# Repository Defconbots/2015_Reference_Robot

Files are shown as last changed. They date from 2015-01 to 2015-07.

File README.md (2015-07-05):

2015_Reference_Robot
====================

The laser used for the contest is the **50 mW** version of this laser: http://www.civillaser.com/532nm-5mw50mw-ttl-modulation-green-laser-module-dot-16mmx70mm-p-130.html

You'll need a controller to run the robot. The source for the controller can be found in the /hw folder.

Software to run the reference robot is in the /sw/TowerDefenderMkII folder.

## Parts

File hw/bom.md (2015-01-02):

## Laser Driver BOM

|Name |Quantity|Part Number |Distributor|
|:---:|:---:|:---:|:---:|
|JP1 |1 |651-5442251 |Mouser |
|IC1 |1 |895-FT232RL |Mouser |
|X1 |1 |538-47346-1001 |Mouser |
|IC2 |1 |998-MIC5219-3.0YMM  |Mouser |
|C1,C2,C3,C4 |4 |C1608X5R1C106M080AB |Mouser |
|C6 |1 |VJ0603A471KXQPW1BC  |Mouser |

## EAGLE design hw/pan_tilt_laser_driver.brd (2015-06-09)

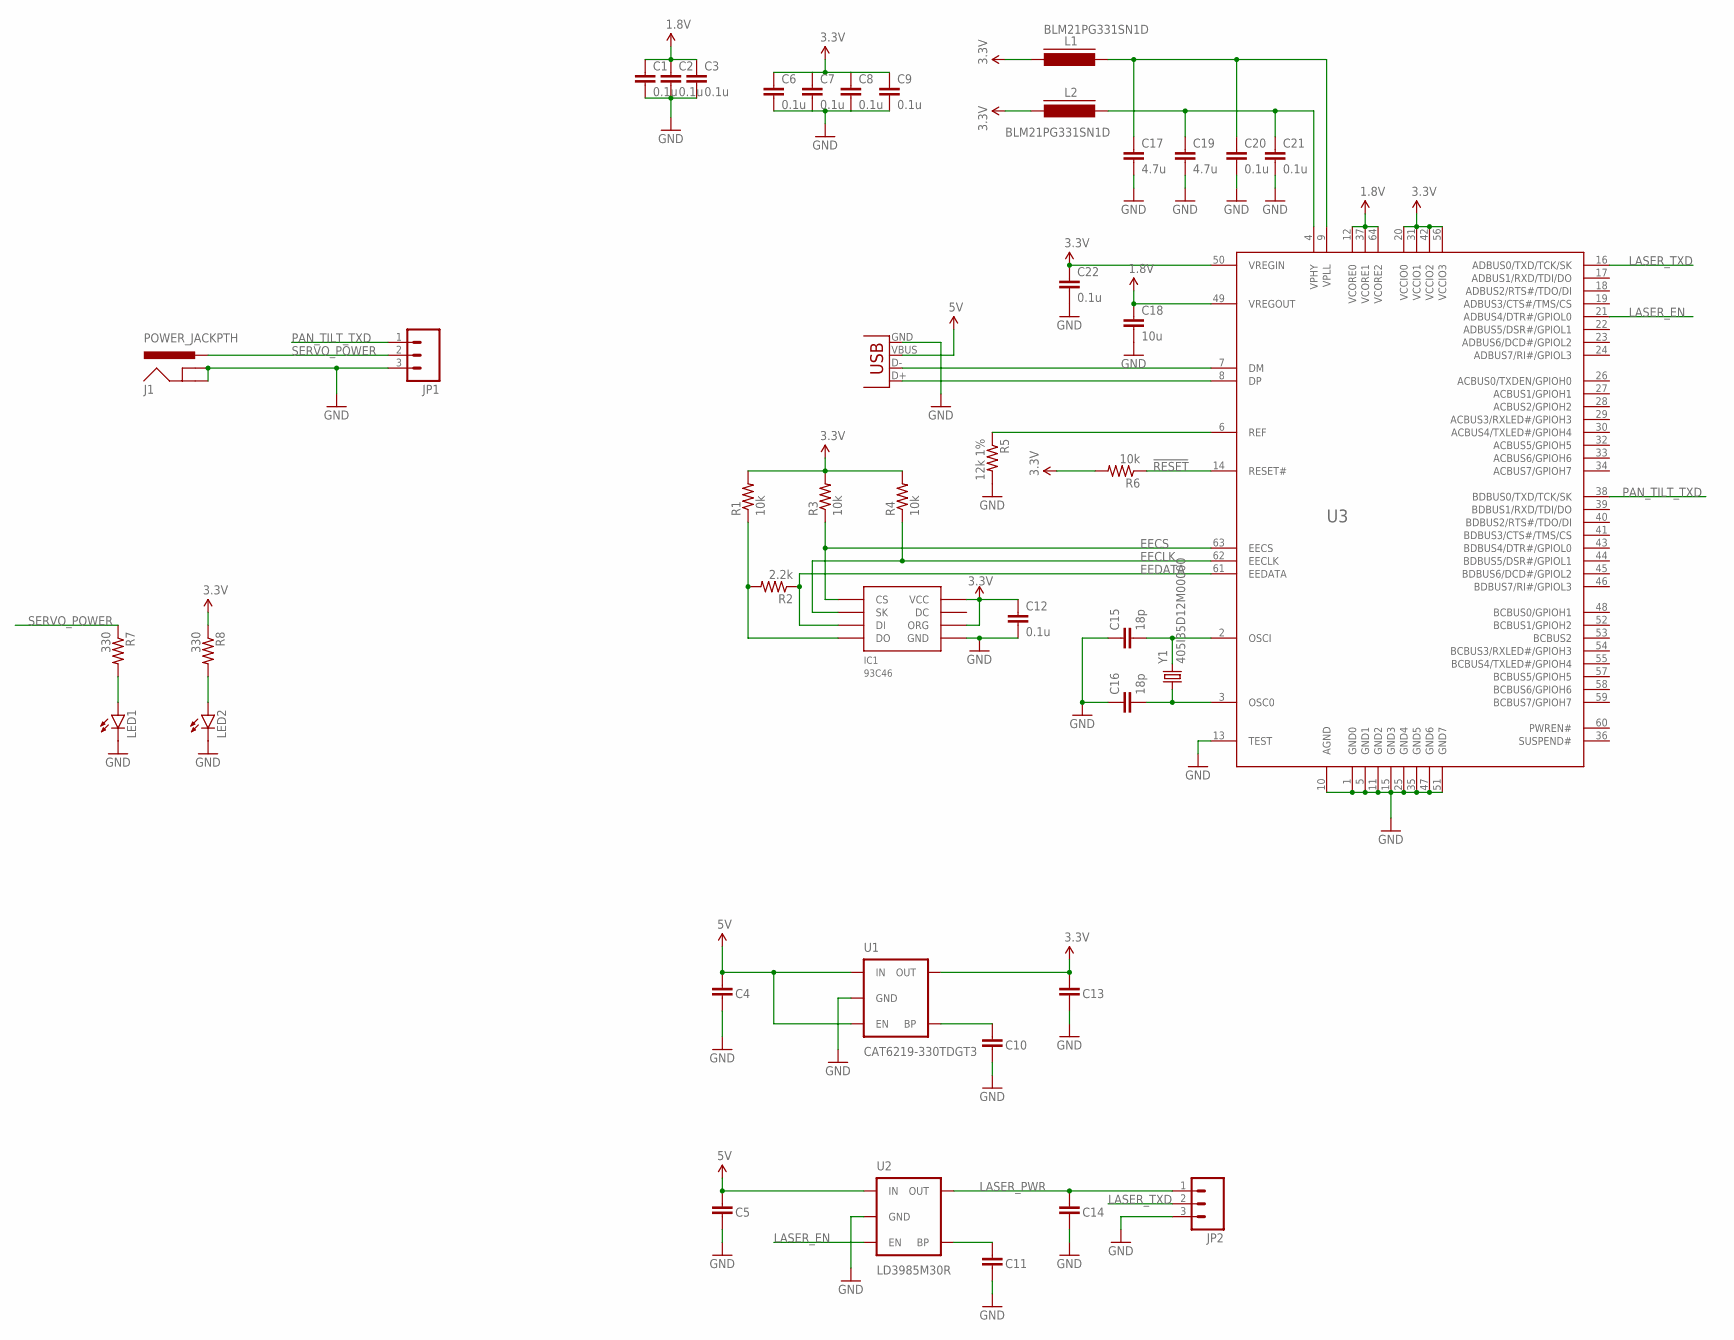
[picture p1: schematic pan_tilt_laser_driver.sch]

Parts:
C1, C2, C3, C6, C7, C8, C9, C12, C20, C21, C22: 0.1u; C0603K
C4, C5, C13, C14: 10u; 0603-CAP
C10, C11: 0.01u; 0603-CAP
C15, C16: 18p; C0603K
C17, C19: 4.7u; C0603K
C18: 10u; C0603K
IC1: 93C46; SOIC8
J1: POWER_JACKPTH; POWER_JACK_PTH
JP1: M0322-03-5035; 22-03-5035
JP2: 651-5442251; SCREWTERMINAL-3.5MM-3
L1, L2: BLM21PG331SN1D; FB805
LED1, LED2: LED1206; LED-1206
R1, R3, R4, R6: 10k; R0603
R2: 2.2k; R0603
R5: 12k 1%; R0603
R7, R8: 330; R0603
U1: CAT6219-330TDGT3; SOT23-5
U2: LD3985M30R; SOT23-5
U3: FT2232H; LQFP64
X1: 538-47346-0001; USB-MICROB
Y1: 405I35D12M00000; CRYSTAL-SMD-5X3

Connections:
1.8V: C1.1, C2.1, C3.1, C18.1, U3.12 (VCORE0), U3.37 (VCORE1), U3.49 (VREGOUT), U3.64 (VCORE2)
3.3V: C6.1, C7.1, C8.1, C9.1, C12.1, C13.1, C22.1, IC1.6 (ORG), IC1.8 (VCC), L1.2, L2.2, R1.2, R3.2, R4.2, R6.2, R8.1, U1.5 (OUT), U3.20 (VCCIO0), U3.31 (VCCIO1), U3.42 (VCCIO2), U3.50 (VREGIN), U3.56 (VCCIO3)
5V: C4.1, C5.1, U1.1 (IN), U1.3 (EN), U2.1 (IN), X1.VBUS
!RESET: R6.1, U3.14 (RESET#)
EECLK: IC1.2 (SK), R4.1, U3.62 (EECLK)
EECS: IC1.1 (CS), R3.1, U3.63 (EECS)
EEDATA: IC1.3 (DI), R2.1, U3.61 (EEDATA)
GND: C1.2, C2.2, C3.2, C4.2, C5.2, C6.2, C7.2, C8.2, C9.2, C10.2, C11.2, C12.2, C13.2, C14.2, C15.1, C16.1, C17.2, C18.2, C19.2, C20.2, C21.2, C22.2, IC1.5 (GND), J1.GND, J1.GNDBREAK, JP1.3, JP2.3, LED1.C, LED2.C, R5.2, U1.2 (GND), U2.2 (GND), U3.1 (GND0), U3.5 (GND1), U3.10 (AGND), U3.11 (GND2), U3.13 (TEST), U3.15 (GND3), U3.25 (GND4), U3.35 (GND5), U3.47 (GND6), U3.51 (GND7), X1.GND
LASER_EN: U2.3 (EN), U3.21 (ADBUS4/DTR#/GPIOL0)
LASER_PWR: C14.1, JP2.1, U2.5 (OUT)
LASER_TXD: JP2.2, U3.16 (ADBUS0/TXD/TCK/SK)
unnamed: C11.1, U2.4 (BP)
unnamed: LED1.A, R7.2
unnamed: U3.7 (DM), X1.D-
unnamed: R5.1, U3.6 (REF)
unnamed: U3.8 (DP), X1.D+
unnamed: C17.1, C20.1, L1.1, U3.9 (VPLL)
unnamed: C15.2, U3.2 (OSCI), Y1.3 (2)
unnamed: C10.1, U1.4 (BP)
unnamed: C19.1, C21.1, L2.1, U3.4 (VPHY)
unnamed: C16.2, U3.3 (OSC0), Y1.1
unnamed: LED2.A, R8.2
unnamed: IC1.4 (DO), R1.1, R2.2
PAN_TILT_TXD: JP1.1, U3.38 (BDBUS0/TXD/TCK/SK)
SERVO_POWER: J1.PWR, JP1.2, R7.1

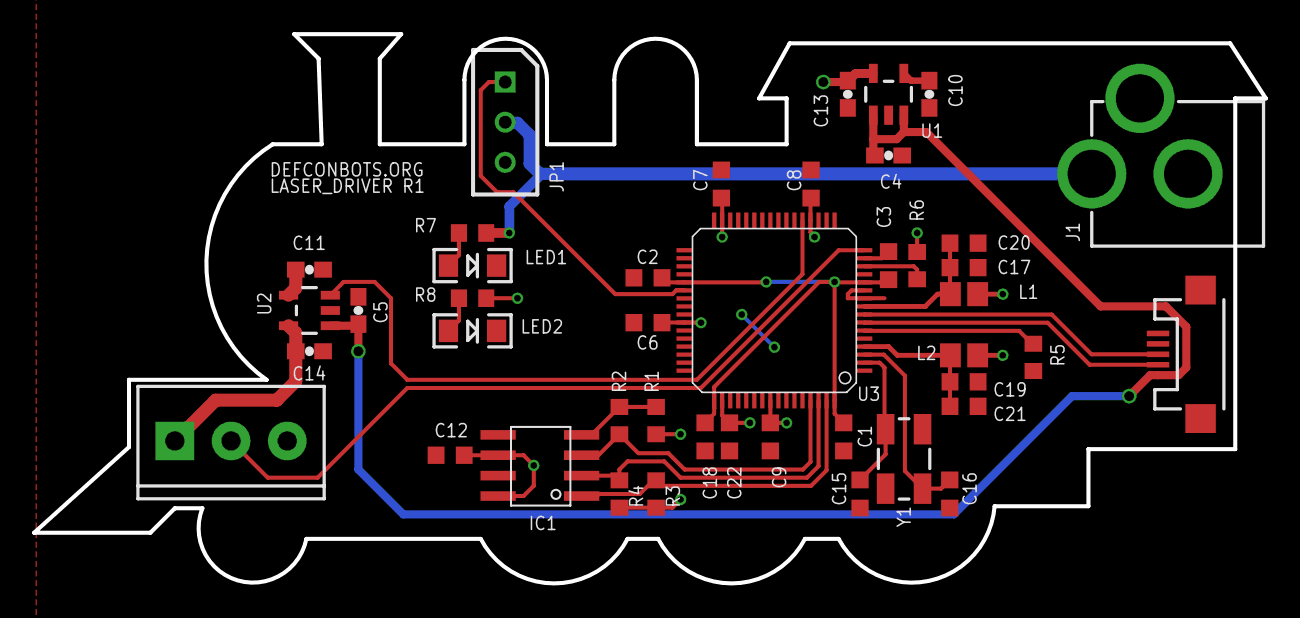
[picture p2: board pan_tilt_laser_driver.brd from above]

Board: 2 copper layers, 76.7 x 34.2 mm, 43 parts (0 on the bottom side), 25 nets.

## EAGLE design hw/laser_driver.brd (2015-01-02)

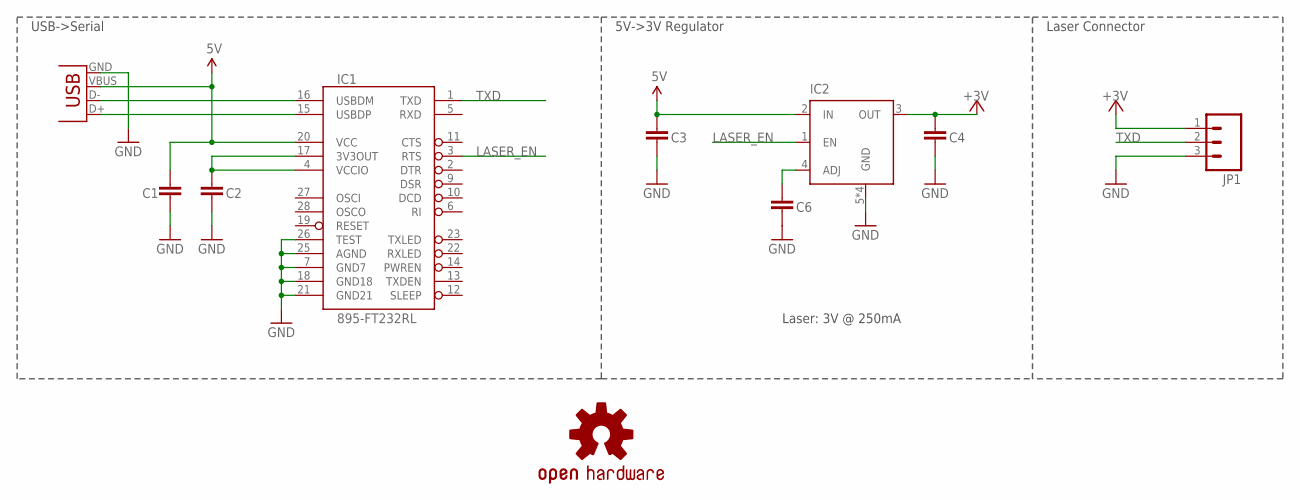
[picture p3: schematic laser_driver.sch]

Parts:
C1, C2, C3, C4: C1608X5R1C106M080AB; 0603-CAP
C6: VJ0603A471KXQPW1BC; 0603-CAP
IC1: 895-FT232RL; SSOP28DB
IC2: 998-MIC5219-3.0YMM; MSOP08
JP1: 651-5442251; SCREWTERMINAL-3.5MM-3
LOGO1: OSHW-LOGOS; OSHW-LOGO-S
X1: 798-ZX62RD-AB-5P8; USB-MICROB

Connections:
3.3V: C2.1, IC1.4 (VCCIO), IC1.17 (3V3OUT)
5V: C1.1, C3.1, IC1.20 (VCC), IC2.2 (IN), X1.VBUS
+3V: C4.1, IC2.3 (OUT), JP1.1
GND: C1.2, C2.2, C3.2, C4.2, C6.2, IC1.7 (GND7), IC1.18 (GND18), IC1.21 (GND21), IC1.25 (AGND), IC1.26 (TEST), IC2.5 (GND), IC2.6 (GND), IC2.7 (GND), IC2.8 (GND), JP1.3, X1.GND
LASER_EN: IC1.3 (RTS), IC2.1 (EN)
unnamed: C6.1, IC2.4 (ADJ)
TXD: IC1.1 (TXD), JP1.2
USB_D+: IC1.15 (USBDP), X1.D+
USB_D-: IC1.16 (USBDM), X1.D-

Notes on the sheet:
USB->Serial
5V->3V Regulator
Laser Connector
Laser: 3V @ 250mA

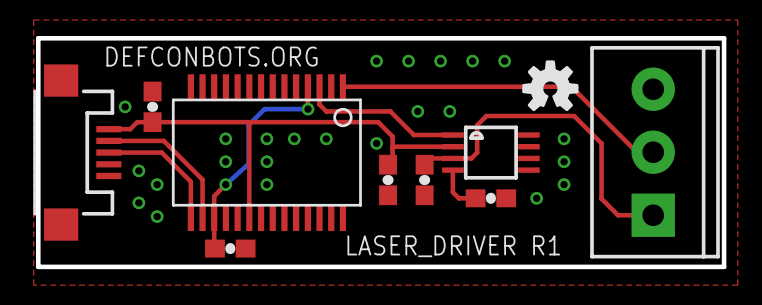
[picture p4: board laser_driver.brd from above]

Board: 2 copper layers, 38.1 x 12.7 mm, 10 parts (0 on the bottom side), 9 nets.

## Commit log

2014-12-05 First pass at laser driver using ft232
    [laser_driver.brd, laser_driver.sch]
2014-12-05 Change connector to terminal block
    [laser_driver.brd, laser_driver.sch]
2014-12-09 Cleanup for fab. Add bom and gerbers.
    [laser_driver.brd]
2014-12-09 Fix noise cap for the regulator
    [laser_driver.brd, laser_driver.sch]
2015-01-02 Fix part numbers for regulator and usb plug. Fix disconnectoed ground pin (4) which was a really stupid mistake...
    [laser_driver.brd, laser_driver.sch]
2015-03-31 Rough schematic with FT2232H
    [pan_tilt_laser_driver.brd, pan_tilt_laser_driver.sch]
2015-04-02 Outline replaced, in progress
    [pan_tilt_laser_driver.brd, pan_tilt_laser_driver.sch]
2015-04-02 Preliminary placement complete.
    [pan_tilt_laser_driver.brd, pan_tilt_laser_driver.sch]
2015-04-03 Round Signal Routing
    [pan_tilt_laser_driver.brd]
2015-04-03 Rough Signal Routing
    [pan_tilt_laser_driver.brd]
2015-04-05 Finished initial routing.
    [pan_tilt_laser_driver.brd, pan_tilt_laser_driver.sch]
2015-05-10 Final version of the ref hw.
    [pan_tilt_laser_driver.brd, pan_tilt_laser_driver.sch]
2015-05-12 Fix the threading
2015-05-15 initial relative control of camera
2015-06-09 Fix part number for USB micro connector (was wrong direction part -- upside down).
    [pan_tilt_laser_driver.brd, pan_tilt_laser_driver.sch]
2015-06-09 Servo connector was backwards. Fixed in schematic and layout.
    [pan_tilt_laser_driver.brd, pan_tilt_laser_driver.sch]
2015-07-05 TowerDefender MkII
    Initial Commit, TowerDefender updated to use 50mW laser

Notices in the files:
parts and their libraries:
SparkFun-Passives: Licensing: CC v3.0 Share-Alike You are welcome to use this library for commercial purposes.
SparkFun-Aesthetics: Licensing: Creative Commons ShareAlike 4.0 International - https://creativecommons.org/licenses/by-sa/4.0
